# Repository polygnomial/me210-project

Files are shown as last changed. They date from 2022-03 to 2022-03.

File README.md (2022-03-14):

# 🐑 ME210 Final Project 🐑
# Team Schleep
_No sheep may leave the flock_
## Meet the Team 🏆
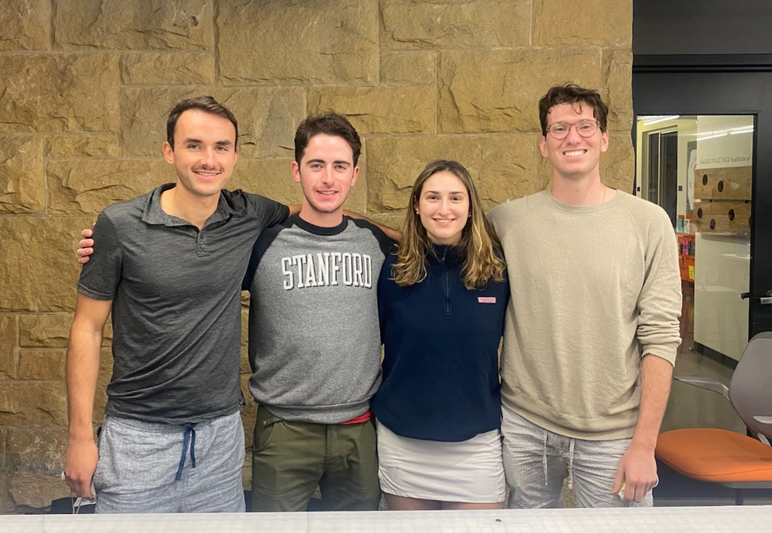
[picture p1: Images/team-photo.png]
Team Photo
*| Paxton: Engineering Physics | 23’
Flynn: Computer Science, 23’ |
D’Arcy: Engineering Physics 22’ |
Grant: Engineering Physics 23’ |*
## Meet the Robot 🤖
Robot Photo
Our task was a simple one—design, build and test a robot for shepherding Stanford sheep (frosh) through their academic careers (from one side of a table to the other). The rules were simple: the robot must fit in a 12” cube. And a bunch of other rules, but details...
#### MVP/Beat the Brick 🧱
For our MVP robot, we used very slow motors, a 3D-printed claw, and a set of 5 IR sensors to navigate through the treacherous maze of Stanford academia.

Three sensors were placed in the center of the robot to sense deviations from the line (career path- CS of course), and two sensors were placed at the far edges of the robot in order to sense junctions and holes in the course. We divided the course up into zones to create a smaller state machine; each zone corresponded to a different ‘trip’ condition for our robot to look out for in order to execute the next turn.

The claw used a servo in order to open and close at the right points in our state machine. To set up this functionality, we had to calibrate the servo to understand what angle corresponded to an open and closed claw. The claw itself used a pair of 3D printed gears to translate the movement of the servo to opening and closing the claw with the right amount of force to trap our ‘sheep’ in their pen without decapitation.

We initially installed faster motors on our robot, however we quickly realized this made it very difficult for us to create reliable line following code. To combat this we switched out our motors for a much slower set without encoders that gave the robot enough time to react to deviations in the path (sophomore year crisis when they think they might do Symbolic Systems instead of CS).

#### State Machine
##### MVP
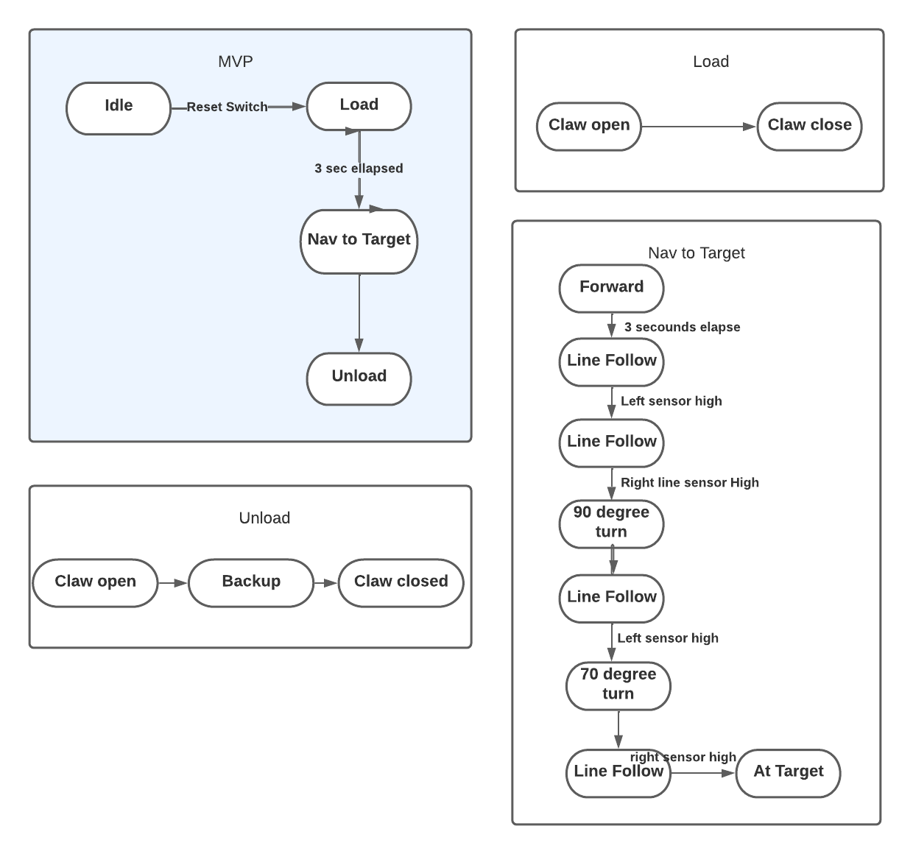
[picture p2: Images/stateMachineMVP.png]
MVP_State


##### Competition Robot
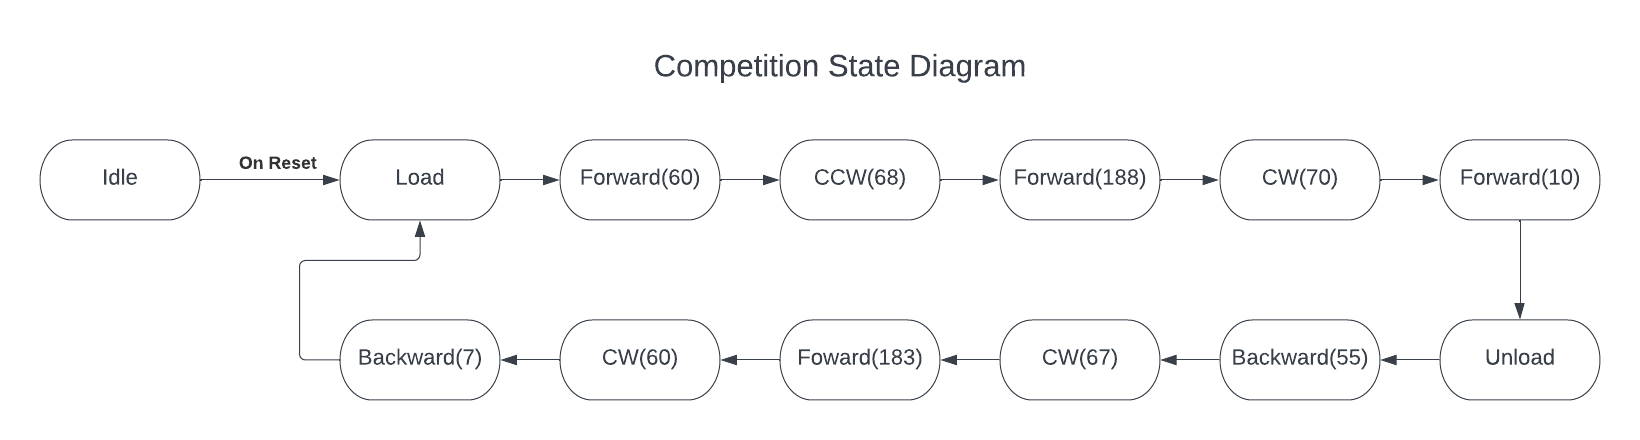
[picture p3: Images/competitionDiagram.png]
Final_State


## MVP Subsystem Overviews

### Mechanical

CAD is available [in Fusion 360 format](./CAD/Assembly.f3z) and as a [STEP file](./CAD/Assembly.step). These may be used to modify the design or generate STLs for printing and DXFs for laser cutting. View the CAD online in 3D [here](https://a360.co/3q2kXgB)

##### Chassis

Our chassis design went through three iterations. The first iteration was very simple. It consisted of a rectangle with attachment points for the wheels and claw. By the second iteration, we added more space for electronics which we were taping on originally. We also added a  mechanism for attaching line sensors to the bottom of the chassis. The second iteration also had a second layer that connected to the first layer with laser cut standoffs. While the second iteration began looking like a robot, it was relatively messy mechanically. The laser cut standoffs introduced significant play into the design and the sensors on the bottom (which were also a friction fit of laser cut pieces) kept on falling out. Additionally our electronics were still mostly mounted on a breadboard that was taped to the second layer. Debugging became very challenging as our design increased in complexity. We designed our third iteration to address many of the pain points introduced by the second. We started using 3D printed standoffs with bolts in order to create a more secure attachment between the different layers. Similarly, we moved over to entirely 3D printed sensor mounts that were also attached to the chassis with bolts. In addition to the more secure attachment points, we added attachment points for the motor driver and bread board to create a more clean design and simplify debugging. We finally added a spot for the power switch and holes to pass the wires through.

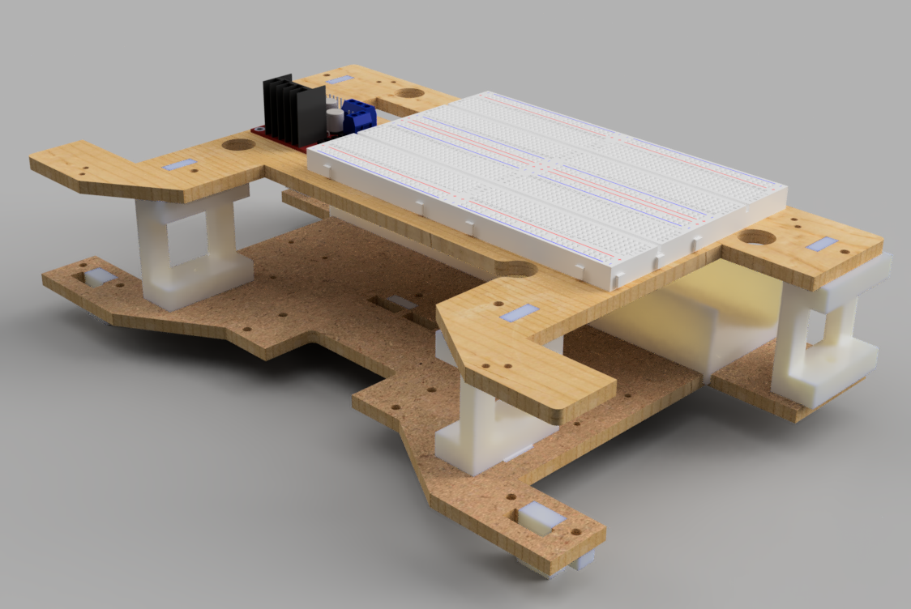
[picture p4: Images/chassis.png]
Chassis


##### Claw

While brainstorming for a ball mechanism, we wanted to design something that was simple but also general enough to handle the large megasheep and the action of lifting. The mechanism we came up with was a claw actuated by a single servo with interlocking gears to make both sides of the claw move in tandem. We printed out two iterations of the claw in order to fine tune the shape and mechanism. For the second iteration, we made the claw slightly more compact in the forward-backward direction, increased the slope inside the claw to guarantee that the balls would roll out when it opened, and created a more stable mechanism for attaching the servo to the gear.

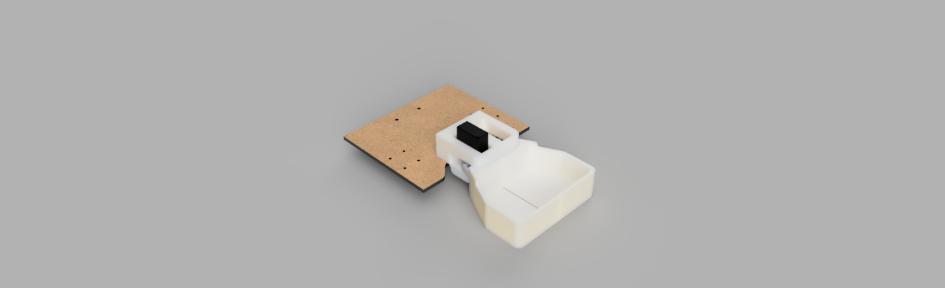
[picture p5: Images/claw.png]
Claw

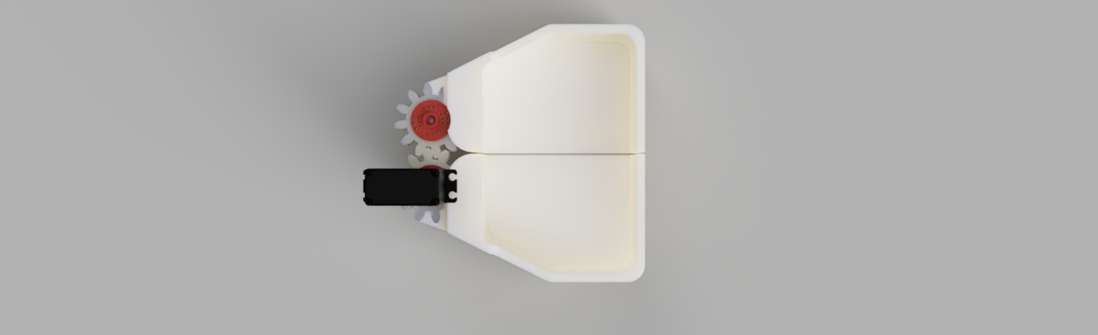
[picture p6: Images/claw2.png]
Claw Mech


##### Crane

We designed a very large mechanism for moving the claw 12” up to a basket for double points. To achieve this, we decided to mount the claw on linear bearings and lift it with a stepper motor paired and a timing belt similar to how many 3D printers work. The official rules stated “your robot may be dismembered to conform to this specification”—this was a point of contention among many of the contenders. We interpreted this as “your robot may have some of its members detach during the weigh-in (fitting)”. The referees ruled that this interpretation was fraught, so we descoped this subsystem. Do datasheets have jokes in them? That would be funny.

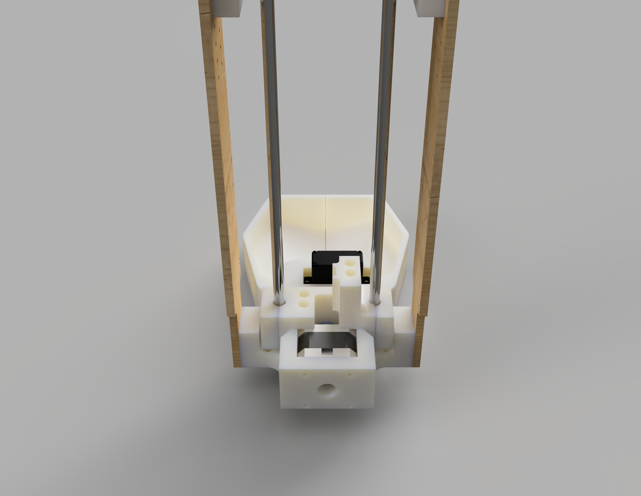
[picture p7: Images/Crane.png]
Crane


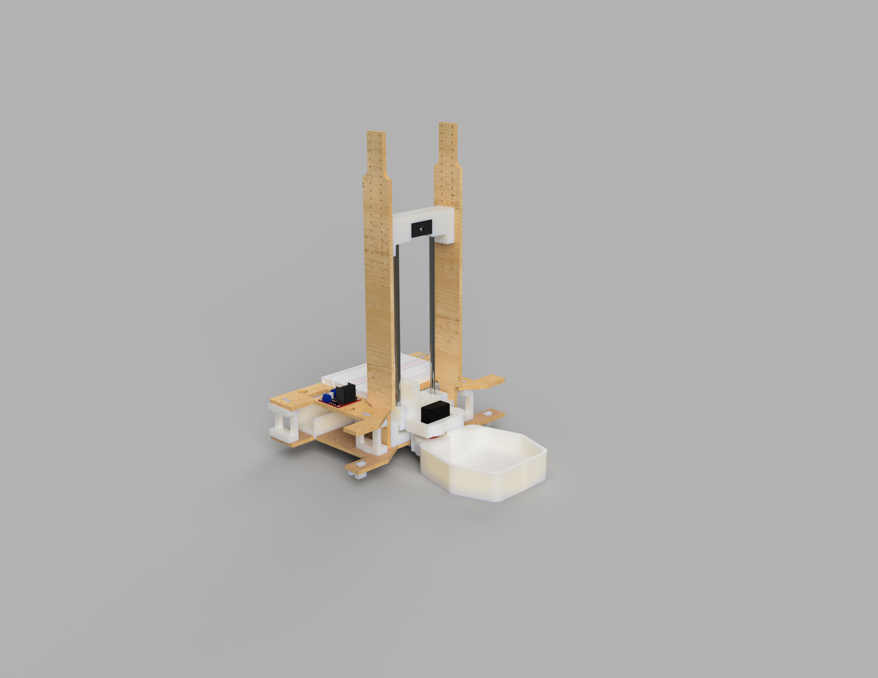
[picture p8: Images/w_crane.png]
Full Design


#### Electrical ⚡
##### Power
We chose to use a baseline of +7.2V to power the robot with two batteries in parallel instead of +14.4V in series due to the input ratings of our voltage converter. We actually only used one battery the entire time and simply recharged it to keep the structure smaller and wiring simpler, but if we had a few more days to implement our other systems, we would have used two in parallel to keep the system operating voltage more consistent. The only MVP system directly connected to 7.2V is the main motor driver, all other systems use voltage from our two voltage converters.

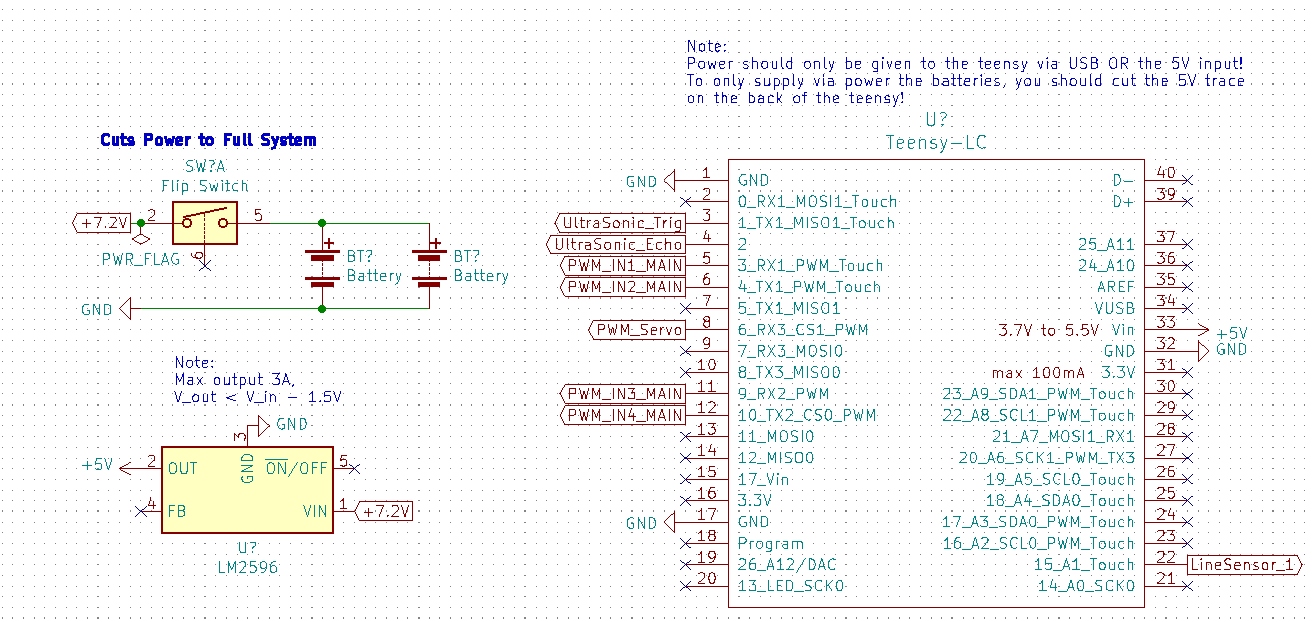
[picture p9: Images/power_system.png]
Power System
*Note: ignore Teensy data connections, this is just to demonstrate our power systems*

We used the LM2596 to create a +5V output to power the Teensy LC with the back USB trace cut so that we ensured consistent ground and power sources (avoiding computer power supply) and only used the USB input for TX/RX. We used the Teensy incorporated 3.3V converter to create a 3.3V power line. We were very careful to not over draw current from these two power converters, and if we were to implement our elevator design, we would have added a second LM2596 converter to remain within the 3A maximum rating.

#### Motors
We initially began our MVP design with larger drive motors (Gear Motor w/Encoder, model No.GB37Y3530-12V-251R) with embedded encoders, but these motors were too fast for our three central line sensors to maintain stable line following, so we changed to smaller motors without encoders for our checkoff where we used a line following method. Abandoning line sensing after our checkoff for more exciting navigation techniques, we changed our motors again for the encoder motors for increased torque and speed. Our two chassis motors are driven by the L298N motor driver in an H-Bridge configuration with PWM control from the Teensy.

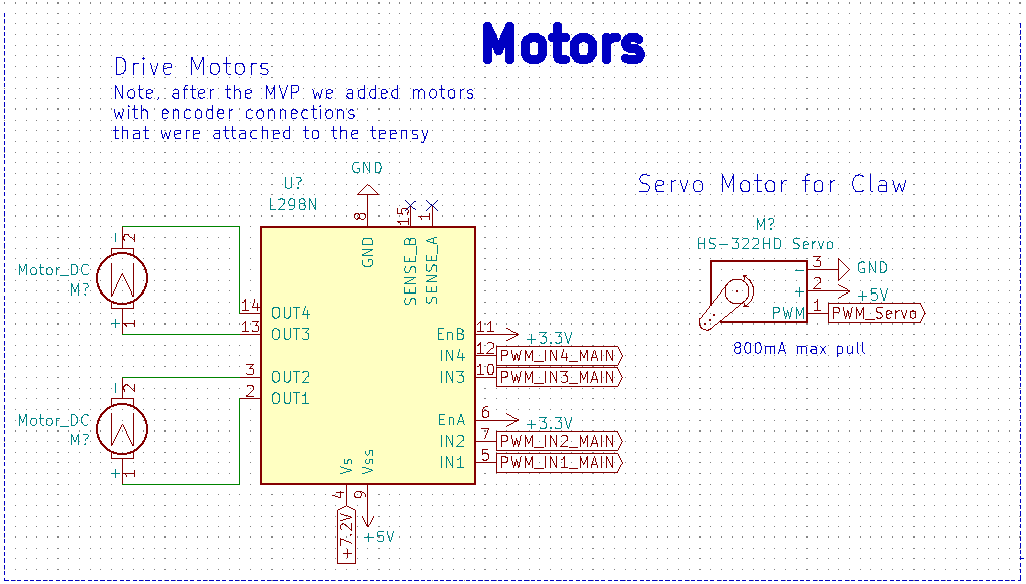
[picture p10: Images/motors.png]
Motors
*Note: Doesn't include non-MVP stepper motor and associated voltage converter*

The collection claws are driven by a small HS-322HD servo motor, which we could easily write to open and close and specific angles. The motor provided far enough torque to close the claw. One challenge was that we had to change the given “close” and “open” angles each time we rebuilt the claw due to the servo motor’s reference angle changing.

We had one final stepper motor (not included on the schematic) that ran our elevator up and down to exact heights. This stepper design was almost identical to that of Lab 2, but we had inconsistent behavior because our draw voltage of 7.2V was a bit too low for the stepper. We added a voltage converter to increase the input voltage, which fixed inconsistencies with the stepper.

#### Line/Hole Sensors
We used the IR reflection sensors available in the lab (QRB1134) to implement a line following system. Testing the lab conditions and the height of our chassis, we finalized on an emitter load resistor of 100 ohms and a collector load resistor of 50k ohms. This allowed us to differentiate black tape from white floor and was sensitive enough to differentiate hole from black tape for hole detection.

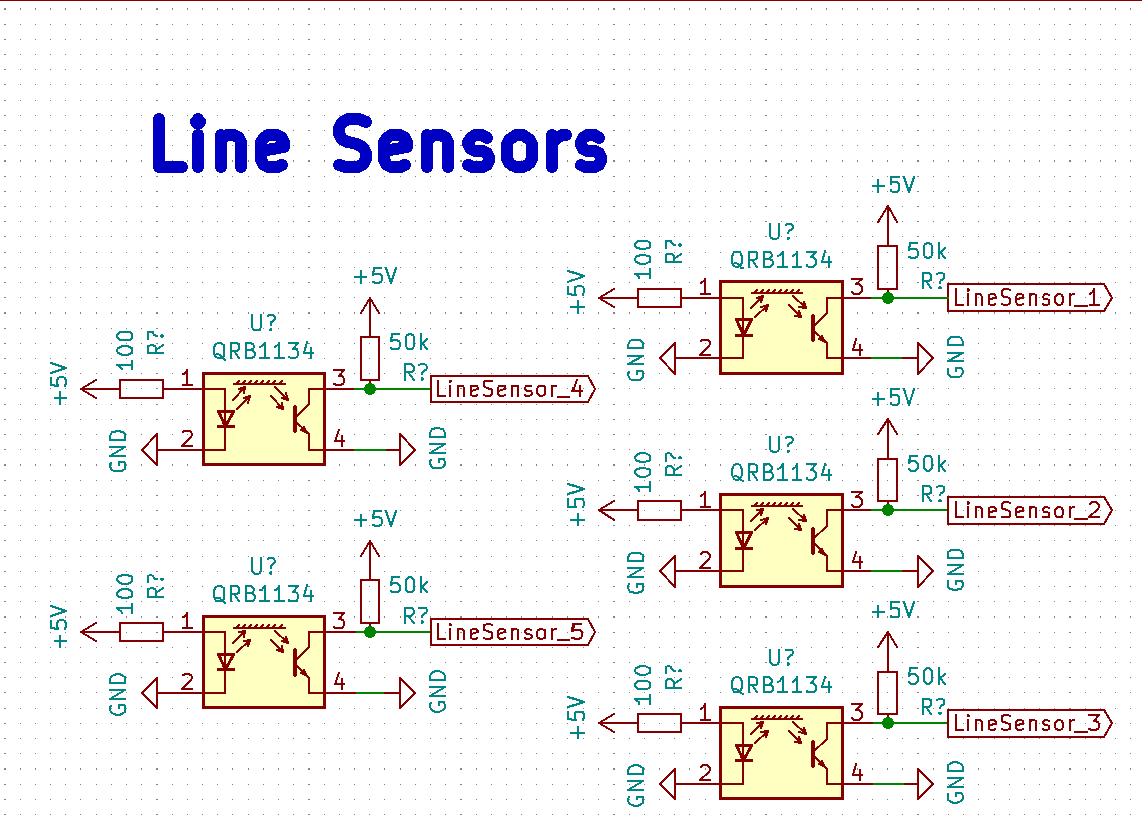
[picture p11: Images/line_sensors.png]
Line_Sensors


#### Beacon Sensors (De-Scoped)
The last two weeks of the project after we were confident in our MVP, our team changed from a line following strategy to a beacon sensing approach while we developed the elevator system to deliver balls to the upper basket. We found several challenges in the beacon sensing and only got the sensors to work reliably two days before the competition once it was too late to fully implement the technology. However, we built and successfully tested four of the beacon sensors and developed simple code that read the modified signal to determine the frequency and therefore the beacon “color”. All beacon sensor designs used the LTR-3208E phototransistor attached to a transresistive amplifier that linearized the output signal from the LTR. We also noticed a pervasive low frequency signal that was easily filtered out on both designs by a single passive RC high pass filter with Fc = 160 Hz.

Our first approach to beacon sensing that we ultimately abandoned due to the complexity of the circuit was a selective filtering approach that filtered out one of the beacons and only returned a binary high/low voltage depending if the other beacon was in sight. We fully built out a model for the 910 Hz signal and successfully tested it, but the amount of components required for the circuit and the need to build one for red and one for blue led us to choose a different beacon sensing option. However, this complex circuit was a really fun challenge.

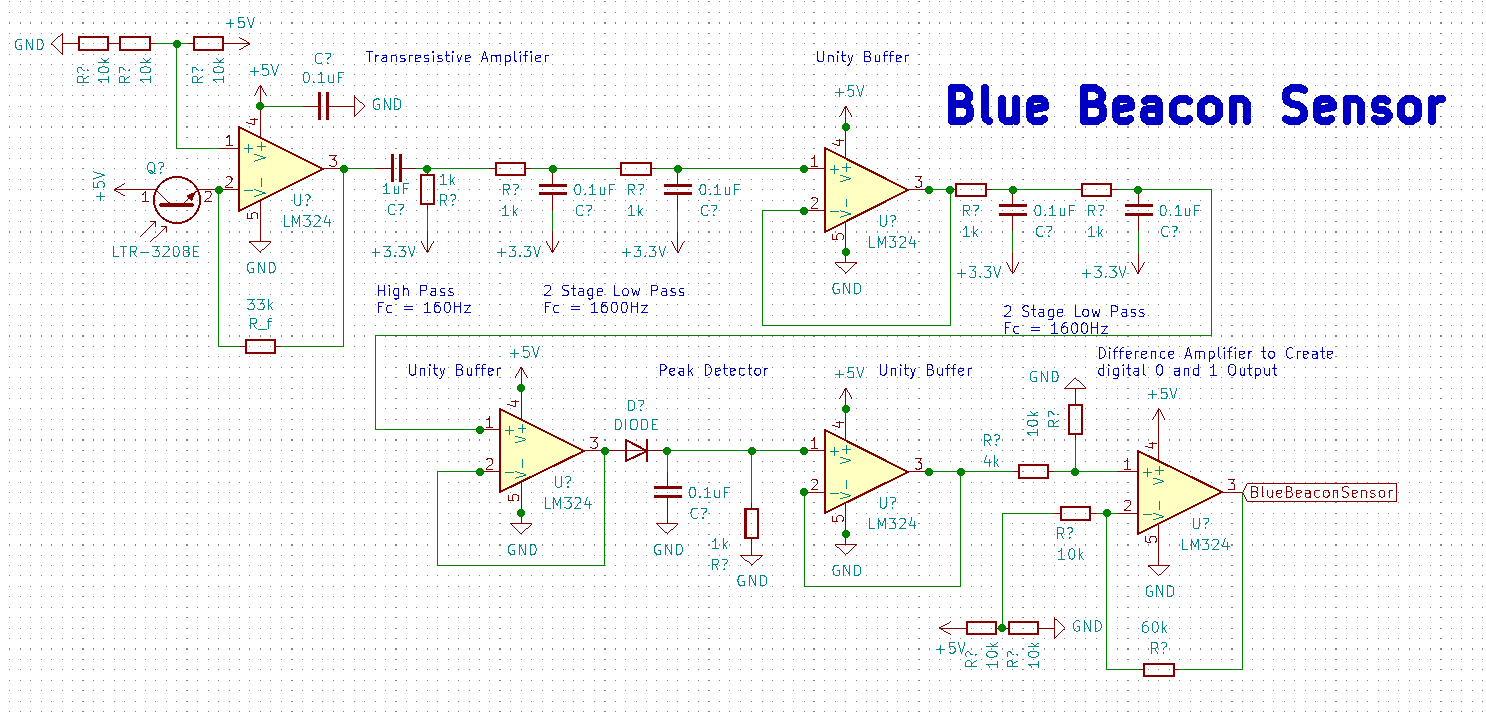
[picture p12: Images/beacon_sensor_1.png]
Beacon_Sensor_1
*First beacon sensor design*

After the transresistive amplifier and high pass filter, we added two 2-stage low pass filters separated by a unity buffer to eliminate the 3333 Hz red signal. The 3333 Hz signal was far stronger than the 910 Hz signal for some reason, so we had to use two steep cutoffs to dampen the signal well. Additionally, we had the RC filters pull the signal average to 3.3V to be within the operating range of the opamp which would otherwise clip the signal at 0V. After the second 2-stage filter, we added another unity buffer and then a peak detector circuit that would keep only the high signal of about 3.5V when pointed at 910 Hz compared to 3V without signal. I had to add a load resistor to the peak detector connected to ground to solve capacitance loading issues after adding another unity buffer after the peak detector. Finally, to turn the 3V no-signal, 3.5 V signal output to 0 V no-signal, 3.3 V signal, I added a difference amplifier circuit to return the final signal as a digital 1 or 0 output voltage. One change I would add to this circuit is adding another unity buffer to the references of the RC passive filters. Here’s the final product:

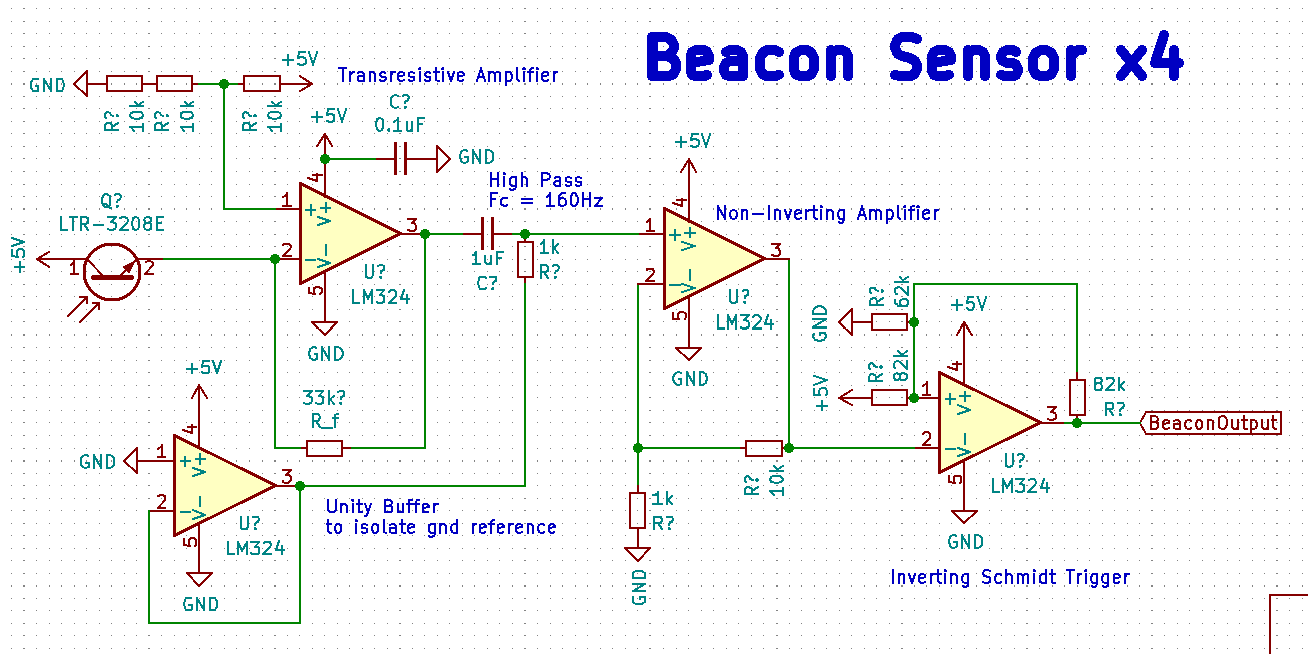
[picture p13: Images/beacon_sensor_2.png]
Beacon_Sensor_2
*Final beacon sensor design*

The circuit we actually ended up using simply returned a filtered, amplified signal of the raw frequency output, which we could connect to the teensy to determine if the input signal is 3333 Hz or 910 Hz. for this circuit the aim was to make the entire circuit use only one four stage opamp package. This circuit uses a unity buffer attached to ground as a reference to the high pass filter. Then the signal is fed into a simple non-inverting amplifier and finally into an inverting Schmitt trigger that adds correcting hysteresis to smooth out the output frequency. This circuit outputted beautiful signals that accurately provided pointing data, but it again suffered from the fact that the 3333 Hz signal was far brighter and would interfere with the 910 Hz signal. We also noticed that the white board reflected the signals a bit which led to messy measurements if the phototransistor was pointed too close to the ground.

#### Ultrasonic Sensors (De-Scoped)
Although we didn’t use them for the MVP or contest, we had planned on using the lab provided HC-SR04 ultrasonic sensors to determine distance to a wall and for the elevator to determine if it was in front of the upper basket. We got the sensors reading out distance but did not incorporate them into our abstracted code. Find the basic schematic on our github.

#### Implementation
We used only breadboards for all electronics, which actually worked great and allowed us to modify circuits along the way. To simplify the wiring, we heat shrinked longer wires. See our final wiring here with the beacon sensors attached at the side.

Wiring*We would have heat shrunk the longer wiring here used for the beacon sensors, but we abandoned these the night before the competition to simply use motor encoders*

#### Software 💻

##### Abstraction

To make our code modular and abstract out lower level functionality, we implemented a multple levels of abstraction. The highest level was the '''system.h''' class which included instantiation of a Chassis class (to handle robot wheel actuation), a Claw class, and Sensors struct with all of our sensors.

```

struct System
{
public:
  struct Sensors
  {
    struct LineSensors
    {
      LineSensor left = LineSensor(LINE_LEFT);
      LineSensor center_middle = LineSensor(LINE_CENTER_MIDDLE);
      LineSensor center_left = LineSensor(LINE_CENTER_LEFT);
      LineSensor center_right = LineSensor(LINE_CENTER_RIGHT);
      LineSensor right = LineSensor(LINE_RIGHT);
    };
    LineSensors line;

    struct UltrasonicSensors
    {
      UltrasonicSensor front = UltrasonicSensor(15);
      UltrasonicSensor periscope = UltrasonicSensor(15);
    };
    UltrasonicSensors ultra;
  };
  Sensors sensors;
  Chassis chassis = Chassis(RIGHT_FORWARD_PIN,
                            RIGHT_BACKWARD_PIN,
                            LEFT_FORWARD_PIN,
                            LEFT_BACKWARD_PIN,
                            ENCODER_RIGHT_PIN1,
                            ENCODER_RIGHT_PIN2,
                            ENCODER_LEFT_PIN1,
                            ENCODER_LEFT_PIN2,
                            HUB_TO_HUB_DISTANCE,
                            WHEEL_CIRCUMFERENCE,
                            MOTOR_MIN_SPEED);
  Claw claw = Claw(SERVO_PIN, OPEN_CLAW_ANGLE, CLOSE_CLAW_ANGLE);

  void activity(void);
};

extern struct System shephard;
```

The Chassis class held instantiation of a Motor class or an EncoderMotor class which is a subclass of Motor with added functionality to handle checking the hall sensors used by the encoder. Within the Sensors struct, we instantiate all of our sensor classes which each provided simple interfaces to get data from the sensors. For instance, within the linesensor class we have the function

```
int LineSensor::read()
{
  int value = 0;
  for (int i = 0; i < 10; i++)
  {
    value += analogRead(pin);
  }
  value /= 10;

  if(value <= lineThreshold){
    return 0;
  }
  else{
    return 1;
  }
}
```

which uses a simple sensor averaging technique to reliably return a binary response indicating weather the sensor is over black tape or not.

##### State Machine Implementation

To handle the state machine implementation, we used a similar model to the state machine from the first lab.

```
  switch(state) {
    case STATE_IDLE:
      shephard.chassis.stop();
      break;
    case STATE_LOAD:
      handleLoadState();
      break;
    case STATE_NAV_TARGET:
      handleNavTargetState();
      break;
    case STATE_UNLOAD:
      handleUnloadState();
      break;
    case STATE_NAV_LOAD:
      handleNavLoadState();
      break;
    default:
      Serial.println("What is this I do not even...");
  }
  ```

  In essence, we used a state variable and switch statement to call different handlers depending on which state we were in.

## Competition Robot
Mere days before the competition, after a 1am caffeine fueled work session, various members of our team came to the depressing realization that neither the crane nor the beacon sensors were going to work in time for the Final Competition. Consequently we returned to our MVP, and brainstormed different ways to make our beautiful robot ready for the real world. This took the form of returning to the faster motors, but this time we decided to make full use of the encoders. As our encoders were relatively accurate, we were able to zoom across the obstacle course, ignoring the lines and the holes, taking 22 units every quarter to place our Stanford sheep in their pen (Facebook/ Microsoft/ Google internships). We tried to use the encoders to return our robot to their starting position, however this movement was much less accurate due to the variability of the board, the robot starting position and how the robot turned. If we had more time (like 3 more hours) we would have combined our line sensing with the encoders in order to ensure that our robot returned to the exact same position each time.

## Lessons Learned
While our team started off strong, we hit a number of issues along the way that impeded our progress and might have been avoided.

We were quickly able to identify an MVP and define how we wanted to meet all of our different priorities for the "beat-the-brick" version of our robot. Consequently, we were able to reach our check off point relatively quickly as we all worked efficiently and cohesively to meet this goal. However after this point we failed to have another proper strategy meeting where we decided exactly what our priorities were for our final competition robot. Between our check off point and the competition we all worked on different aspects of the design that eventually failed to come together, forcing us to revert to just using encoders and the claw to score points during the competition. Reflecting on this experience it is clear that one of two strategy meetings with the entire team present would have been enough to streamline our goals and ensure our work was cohesive enough to deliver a final competition-ready robot that utilized a choice set of subsystems.

Practically, we also learnt that 3D printing components can be much more flexible and efficient as this mode allows geometries that have 90 degree angles (such as custom brackets), as well as other custom geographies. We also learnt the importance of reading the design specifications very carefully, as this unfortunately limited our design very late in the competition.

## Build our Robot!
If you would like to build our robot, all the necessary schematics, CAD, and code is available on our github repository linked at the top of this webpage. Feel free to reach out about specific questions and components if not mentioned above. Note: for code run during competition and not MVP check out the hardcode branch on github. :- )

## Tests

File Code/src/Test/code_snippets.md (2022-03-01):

# Quasi Regression Testing

(meant to help debug whether issues stem from electrical or code changes)

## Test Encoder Funcionality

### Using shephard

```c++
#include "Test.h"
#include "System.h"

void setup()
{
    Serial.begin(9600);
    Serial.println("Encoder Test:");
}

long positionLeft = -999;
long positionRight = -999;

void loop()
{   
    shephard.activity();
    long newLeft, newRight;
    newLeft = shephard.chassis.left.get_pos();
    newRight = shephard.chassis.right.get_pos();
    if (newLeft != positionLeft || newRight != positionRight)
    {
        Serial.print("Left = ");
        Serial.print(newLeft);
        Serial.print(", Right = ");
        Serial.print(newRight);
        Serial.println();
        positionLeft = newLeft;
        positionRight = newRight;
    }
}
```

### Without Shephard

```c++
#define ENCODER_OPTIMIZE_INTERRUPTS
#include <Encoder.h>

#define ENCODER_RIGHT_PIN1 8
#define ENCODER_RIGHT_PIN2 11
#define ENCODER_LEFT_PIN1 5
#define ENCODER_LEFT_PIN2 7

Encoder knobLeft(ENCODER_LEFT_PIN1, ENCODER_LEFT_PIN2);
Encoder knobRight(ENCODER_RIGHT_PIN1, ENCODER_RIGHT_PIN2);

void setup() {
  Serial.begin(9600);
  Serial.println("TwoKnobs Encoder Test:");
}

long positionLeft  = -999;
long positionRight = -999;

void loop() {
  long newLeft, newRight;
  newLeft = knobLeft.read();
  newRight = knobRight.read();
  if (newLeft != positionLeft || newRight != positionRight) {
    Serial.print("Left = ");
    Serial.print(newLeft);
    Serial.print(", Right = ");
    Serial.print(newRight);
    Serial.println();
    positionLeft = newLeft;
    positionRight = newRight;
  }
  // if a character is sent from the serial monitor,
  // reset both back to zero.
  if (Serial.available()) {
    Serial.read();
    Serial.println("Reset both knobs to zero");
    knobLeft.write(0);
    knobRight.write(0);
  }
}
```

## Test Motor Funcionality

### With Motor Class

```c++
#include "Test.h"
#include "../Actuators/Motor.h"

#define RIGHT_BACKWARD_PIN 3
#define RIGHT_FORWARD_PIN 4
#define LEFT_BACKWARD_PIN 9
#define LEFT_FORWARD_PIN 10

#define ENCODER_RIGHT_PIN1 8
#define ENCODER_RIGHT_PIN2 11
#define ENCODER_LEFT_PIN1 5
#define ENCODER_LEFT_PIN2 7

Motor motor_l(LEFT_FORWARD_PIN, 
              LEFT_BACKWARD_PIN,
              ENCODER_LEFT_PIN1,
              ENCODER_LEFT_PIN2);

Motor motor_r(RIGHT_FORWARD_PIN, 
              RIGHT_BACKWARD_PIN,
              ENCODER_RIGHT_PIN1,
              ENCODER_RIGHT_PIN2);

int i = 0;
bool debug = false;

void setup(){
    Serial.begin(9600);
    delay(2000);
    motor_r.ccw(90, 50);
    motor_l.ccw(90, 50);
}
void loop(void){
    if (i%100000000 == 0){
        debug  = true;
    } else {
        debug = false;
    }
    motor_l.activity(true);
    motor_r.activity(true);
}
```

## Claw

### With Shephard

```c++
#include "Test.h"
#include "System.h"

unsigned start;

void setup(){
    Serial.begin(9600);
    Serial.println("Currently doing some testing...");
    delay(1000);
    start = millis();
}
void loop(void){
    shephard.activity();
    uint32_t tick = millis();
    Serial.println(tick);
    if (tick - 5000 > start){
        shephard.claw.close();
    } else if (tick - 4000 > start){
        shephard.chassis.move_forward(5, 100);
    } else if (tick - 3000 > start){
        shephard.claw.open();
    }
}
```

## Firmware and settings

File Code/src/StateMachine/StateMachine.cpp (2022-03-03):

#include "StateMachine.h"

#define VELOCITY 255

#define Right_TURN_TIME       4000
#define SECOUND_TURN_TIME     2500

States_t state;
States_r line_state;
Zones_t zone;

unsigned long state_time;
unsigned long serial_time; 
unsigned long curr_time;
unsigned long zone_time;

uint8_t servoPin = 6;
uint8_t servoPos = 0;

uint8_t flagLeftLine = 0;
uint8_t flagRightLine = 0;

unsigned long flag_time;

void setup() {
  // put your setup code here, to run once:
  Serial.begin(9600);
  shephard.claw.open();
  while(!Serial);
  //delay(10000);
  delay(3000);
  //times
  curr_time = millis();
  serial_time = millis();
  state_time = millis();
  flag_time = millis();

  

  changeStateTo(STATE_LOAD);
  
  Serial.println("Setup Complete!");
}

void loop() {
  curr_time = millis();
  checkGlobalEvents();
  checkFlags();
  checkForZoneChange();

  // TO LINE FOLLOW: Must be in state = state_nav_target

  switch(state) {
    case STATE_IDLE:
      shephard.chassis.stop();
      break;
    case STATE_LOAD:
      handleLoadState();
      break;
    case STATE_NAV_TARGET:
      handleNavTargetState();
      break;
    case STATE_UNLOAD:
      handleUnloadState();
      break;
    case STATE_NAV_LOAD:
      handleNavLoadState();
      break;
    default:
      Serial.println("What is this I do not even...");
  }

  //debug for line sensors
  if (curr_time - serial_time > MILLISECONDS(1/PRINT_FREQUENCY) ){
    Serial.println("---------------");
    //Serial.println("left " + String(shephard.sensors.line.left.read()));
    //Serial.println("right " + String(shephard.sensors.line.right.read()));
    //Serial.println("center left " + String(shephard.sensors.line.center_left.read()));
    //Serial.println("center middle " + String(shephard.sensors.line.center_middle.read()));
    //Serial.println("center right " + String(shephard.sensors.line.center_right.read()));
    //Serial.println("---------------");
    serial_time = curr_time;
  }
}

void handleLoadState(void) {
  unsigned int timeInState = curr_time - state_time;
  if (timeInState < 1000) {
    shephard.claw.open(); 
  } else if (timeInState > 1000 && timeInState < 2000) {
    shephard.claw.close(); 
  } else if (timeInState > 2000  && timeInState < 5000) {
    shephard.chassis.move_forward_at_speed(VELOCITY);
  } else if (timeInState > 5000) { 
    changeStateTo(STATE_NAV_TARGET);
    changeZoneTo(ZONE_1);
  }
}

void handleUnloadState(void) {
  int timeInState = curr_time - state_time;
  if (timeInState < 1000) {
    shephard.claw.open(); 
  } else if (timeInState > 1000 && timeInState < 4000) {
    shephard.chassis.move_backward_at_speed(VELOCITY);
  } else if (timeInState > 4000 && timeInState < 10000) {
    shephard.chassis.turn_left_at_speed(VELOCITY);
  } else if (timeInState > 10000) {
    changeStateTo(STATE_NAV_LOAD);
  } 
}

void handleNavTargetState(void){
  //shephard.chassis.move_forward_at_speed(200);
  //if (millis() - state_time> 5000){
  //  changeStateTo(STATE_IDLE);
  //}    
  unsigned long t = curr_time - zone_time;   
  switch(zone) {
    case ZONE_LOAD:
      break;
    case ZONE_1:
      lineFollow();
      break;
    case ZONE_2:
      lineFollow();
      break;
    case ZONE_3:
      // turn 90 degrees and then line follow
      if (t > 1000 && t < 1000+Right_TURN_TIME) {
        shephard.chassis.turn_right(200);
      } else {
        lineFollow();
      }
      break;
    case ZONE_4:
      // turn less than 90 degrees and then line follow
      if (t < SECOUND_TURN_TIME) {
        shephard.chassis.turn_left(200);
      } else {
        lineFollow();
      }
      break;
    case ZONE_TARGET:
      if (t < 1000) {
        shephard.chassis.move_forward_at_speed(VELOCITY);
      } else {
        changeStateTo(STATE_UNLOAD);
      }
      break;
    default:
      Serial.println("Zone has more states than Paxton thought");
  }
}

void handleNavLoadState(void) {
  shephard.chassis.stop();
}

void checkGlobalEvents(void) {
  if (TestForKey()) RespToKey();
}

void checkFlags(void) {
  if (curr_time - flag_time > FLAG_TIME) {
    flagLeftLine = 0;
    flagRightLine = 0;
  }
}

void checkForZoneChange(void) {
    uint8_t left = shephard.sensors.line.left.read();
    uint8_t right = shephard.sensors.line.right.read();
    //Serial.println(left);
    if (left && zone == ZONE_1) {
      setFlag(flagLeftLine);
      changeZoneTo(ZONE_2);
    } else if (right && zone == ZONE_2) {
      setFlag(flagRightLine);
      changeZoneTo(ZONE_3);
    } else if (left && zone == ZONE_3 && curr_time - zone_time > 5000) {
      changeZoneTo(ZONE_4);
      setFlag(flagLeftLine);
    } else if (left && zone == ZONE_4 && curr_time - zone_time > 6000) {
      changeZoneTo(ZONE_TARGET);
    }
}


void lineFollow(void) {
    uint8_t center_left = shephard.sensors.line.center_left.read();
    uint8_t center_middle = shephard.sensors.line.center_middle.read();
    uint8_t center_right = shephard.sensors.line.center_right.read();
    // primary line sensing states
    if (center_middle && !center_right && !center_left){
      changeLineStateTo(STATE_ON_LINE);
    }
    else if (!center_middle && center_right && !center_left) { 
      changeLineStateTo(STATE_OFF_LEFT);
    }
    else if (!center_middle && !center_right && center_left) { 
      changeLineStateTo(STATE_OFF_RIGHT);
    }
    else if (center_middle && !center_right && center_left && !flagLeftLine) { 
      changeLineStateTo(STATE_OFF_SLIGHT_RIGHT);
    }
    else if (center_middle && center_right && !center_left && !flagRightLine) { 
      changeLineStateTo(STATE_OFF_SLIGHT_LEFT);
    }

    switch(line_state) {
      case STATE_ON_LINE:
        shephard.chassis.move_forward_at_speed(VELOCITY);
        break;
      case STATE_OFF_RIGHT:
        shephard.chassis.veer_forward(250, 180);
        break;
      case STATE_OFF_SLIGHT_RIGHT:
        shephard.chassis.veer_forward(250, 200);
        break;
      case STATE_OFF_LEFT:
        shephard.chassis.veer_forward(180, 250);
        break;
      case STATE_OFF_SLIGHT_LEFT:
        shephard.chassis.veer_forward(200, 250);
        break;
      default:
        Serial.println("humm");
    }

}
  
uint8_t TestForKey(void) {
  uint8_t KeyEventOccurred;
  KeyEventOccurred = Serial.available();
  return KeyEventOccurred;
}


void changeStateTo(States_t s) {
  if (s != state) {
    state = s;
    state_time = curr_time;
  }
}

void changeLineStateTo(States_r s) {
  if (s != line_state) {
    line_state = s;
  }
}

void changeZoneTo(Zones_t z) {
  if (z != zone) {
    zone = z;
    zone_time = millis();
    Serial.println("In new zone " + z);
  }
}

void setFlag(uint8_t flag){
  flag = true;
  flag_time = curr_time;
}

void RespToKey(void) {
  uint8_t theKey;
  theKey = Serial.read();
  Serial.print(theKey);
  Serial.print(", ASCII=");
  Serial.println(theKey, HEX);

  switch(theKey) {
    case ' ': 
      state = STATE_IDLE;
      break;
    case 'r': 
      changeStateTo(STATE_NAV_TARGET);      
      break;
    default:
      break;
  }
}

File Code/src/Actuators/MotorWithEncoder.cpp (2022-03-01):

#include "Arduino.h"
#include "MotorWithEncoder.h"

void MotorWithEncoder::activity(){
  pos = abs(encoder.read());
  
  // overflow protection
  if (pos > 0xFFFFFF){
    overflow +=  abs(encoder.read());
    encoder.write(0);
    pos = 0;
  }
  
  // decide whether to stop
  if ((pos + overflow) > target){
    stop();
  }
}

void MotorWithEncoder::stop(void) {
  analogWrite(f_pin, 0);
  analogWrite(b_pin, 0);
  encoder.write(0);
  overflow = 0;
  pos = 0;
  target = 0;
}

void MotorWithEncoder::move(double angle, uint8_t speed){
  if (angle > 0){
    cw_at_speed(speed);
  } else {
    ccw_at_speed(speed);
  }
  
  target = abs(pos + angle / 360 * 1920);
  if (speed < min_speed){
    speed = min_speed;
  }

  encoder.write(0);
  overflow = 0;
  pos = 0;
}

void MotorWithEncoder::cw(double angle, uint8_t speed){
  move(angle, speed);
}

void MotorWithEncoder::ccw(double angle, uint8_t speed){
  move(-angle, speed);
}

int MotorWithEncoder::get_pos(void){
  return pos;
}

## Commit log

2022-02-17 starting to implement pwm for motors
2022-02-19 Added KiCad Files
    [ME210_Final_Project.kicad_pcb, ME210_Final_Project.sch]
2022-02-23 removing op amp from line sensor
    [ME210_Final_Project.kicad_sch]
2022-02-23 Cleaned up KiCad files
    [ME210_Final_Project.kicad_sch, ME210_Final_Project.sch]
2022-02-24 guess and check claw angles
2022-02-24 adding specific instance of line sensor + small line sensor lib mod
2022-02-26 added sensor class, editing beacon sensor on kicad
    [ME210_Final_Project.sch]
2022-02-26 add gitignore for kicad and friends
2022-02-28 add encoder lib dep
2022-02-28 abstract motors and add encoders
2022-02-28 switch to cw/ccw in Motor and update overflow protection
2022-02-28 add framework for distance based movement
2022-02-28 test motors and chassis
2022-03-01 update claw setpoints
2022-03-01 add test case to markdown file
2022-03-01 continue making non-encoder motor class
2022-03-02 adding a couple comments
2022-03-13 chassis addition
2022-03-14 remove Fusion 360 embed and add broken links for CAD
2022-03-14 add cad and reorganize
    [ME210_Final_Project.kicad_pcb, ME210_Final_Project.sch]
2022-03-14 Finialized website, added correct kicad files
    [ME210_Final_Project.kicad_pcb, ME210_Final_Project.sch]
